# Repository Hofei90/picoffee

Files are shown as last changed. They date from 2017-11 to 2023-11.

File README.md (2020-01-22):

# picoffee
## Kurzbeschreibung
Die Software picoffee steuert die Freigabe für eine Kaffeemaschine bei Anmeldung eines Benutzers mittels 
RFID Chip und ausreichendem Guthaben.
Hardwareumsetzung kann natürlich unterschiedlich ausgeführt sein. In diesem Projekt ist es so realisiert, dass die 
Widerstände der Tastenplatine der Kaffeemaschine entlötet worden sind und diese über Relais zugeschaltet werden, 
gesteuert von picoffee.

## Software
### Benötigte Software
picoffee unterstützt Pythonversion >3.5.x

Benötigte Pythonmodule sind in der _requirements.txt_ gelistet.
 
### Installation
Paket unter gewünschten Verzeichnis abspeichern.

Zum Start von picoffee direkt die Datei _picoffee.py_ starten. Ein Autostart kann z.B mittels Systemd gelöst werden.
Beispiel siehe unter _picoffee.service_

## Komplette Projektvorstellung
Komplette Projektvorstellung unter: https://forum-raspberrypi.de/forum/thread/32856-kaffeemaschine-automatische-abrechnung/

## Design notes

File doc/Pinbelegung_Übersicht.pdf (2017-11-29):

Verwendung | Name | BCM | Pin Pin | BCM | Name | Verwendung
3,3V | 3,3V | - | 1 | 2 | - | 5V | 5V
LCD I²C | SDA | 2 | 3 | 4 | - | 5V | 5V
LCD I²C | SCL | 3 | 5 | 6 | - | GND | GND
| GPIO7 | 4 | 7 | 8 | 14 | TxD
GND | GND | - | 9 10 | 15 | RxD
GPIO0 | 17 | 11 12 | 18 | GPIO1
GPIO2 | 27 | 13 14 | - | GND | GND
GPIO3 | 22 | 15 16 | 23 | GPIO4
3,3V | 3,3V | - | 17 18 | 24 | GPIO5
RF522_MOSI | MOSI | 10 | 19 20 | - | GND | GND
RF522_MISO | MISO | 9 | 21 22 | 25 | GPIO6 | RF522_RST
RF522_SCK | SCLK | 11 | 23 24 | 8 | CE0 | RF522_SDA
GND | GND | - | 25 26 | 7 | CE1 | I_Mahlwerk
I²C | ID_SD | 0 | 27 28 | 12 | ID_SC | I²C
I_Wasser | GPIO21 | 5 | 29 30 | - | GND | GND
O_Freigabe | GPIO22 | 6 | 31 32 | 12 | GPIO26 | I_Taster_minus
O_RGB_R | GPIO23 | 13 | 33 34 | - | GND | GND
O_RGB_G | GPIO24 | 19 | 35 36 | 16 | GPIO27 | I_Taster_plus
O_RGB_B | GPIO25 | 26 | 37 38 | 20 | GPIO28 | I_TasterM
GND | GND | - | 39 40 | 21 | GPIO29 | I_TasterOk
Freie Pins | 9
Verwendete Pin | 31

Pinbelegung Kaffeekontrolle

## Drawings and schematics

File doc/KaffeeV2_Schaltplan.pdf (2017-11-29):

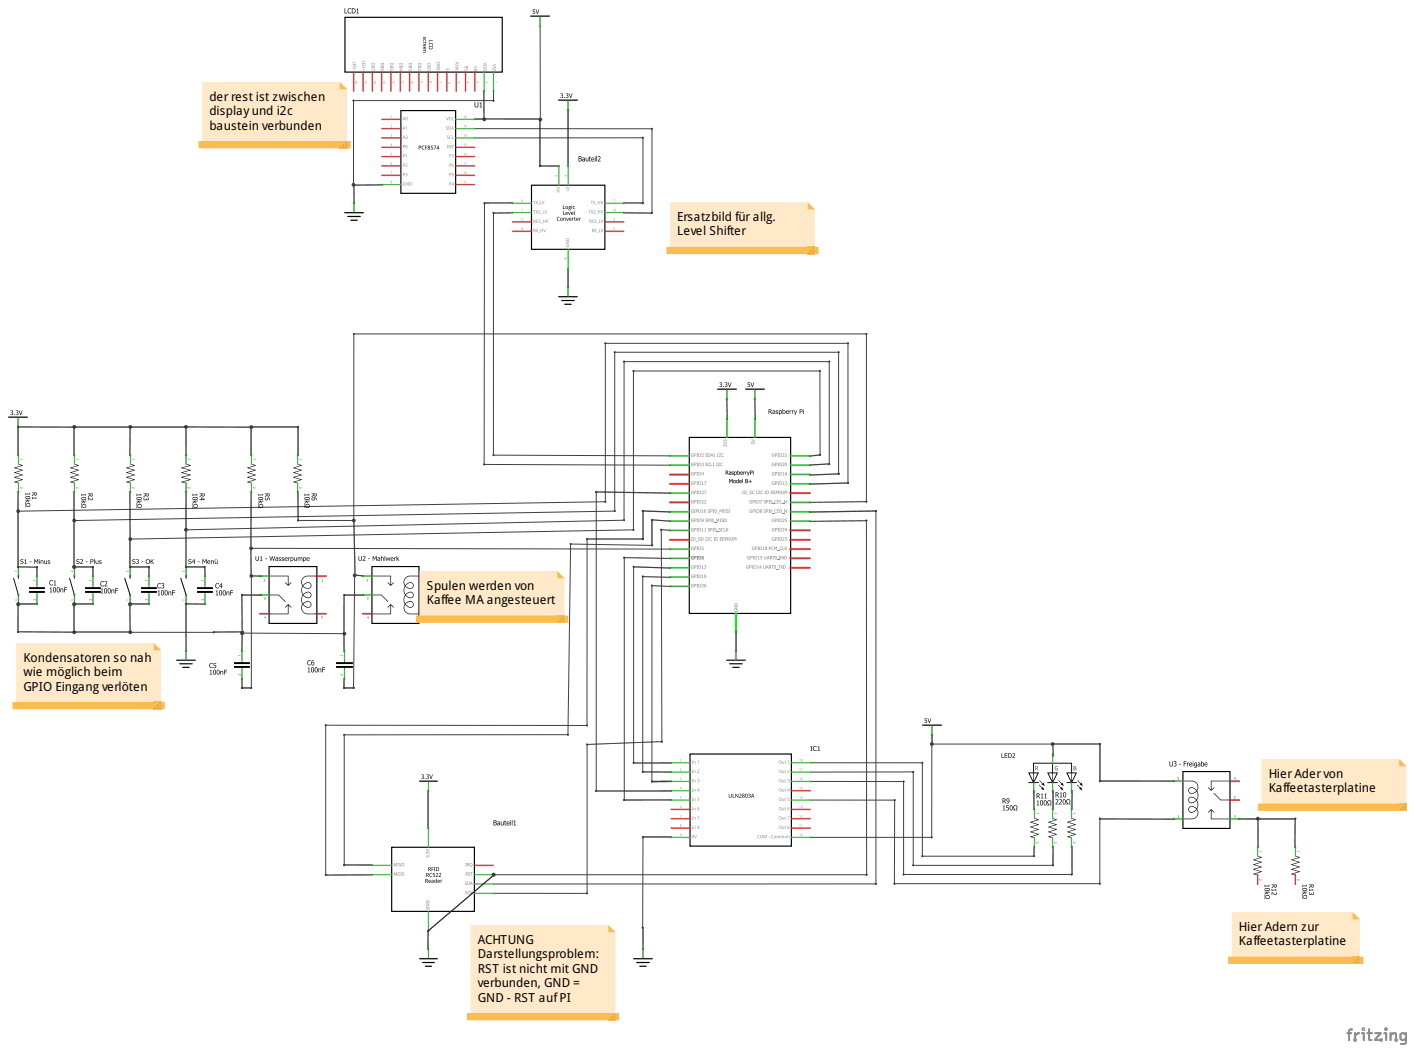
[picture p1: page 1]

derrest ist zwischen
display und i2c
baustein verbunden

Ersatzbild für allg.
Level Shifter

Spulen werden von
Kaffee MA angesteuert

Kondensatoren so nah
wie möglich beim
GPIO Eingang verlöten

Hier Ader von
Kaffeetasterplatine

Hier Adern zur

ACHTUNG
Darstellungsproblem:
RST ist nicht mit GND
verbunden, GND =
GND - RST auf PI

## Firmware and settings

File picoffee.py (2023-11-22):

#!/usr/bin/python3
# -*- coding: utf-8 -*-
# Script zur Kaffeekontrolle

import datetime
import random
import shlex
import signal
import subprocess
import time
from pathlib import Path
from sys import exit

import gpiozero
import toml
from RPLCD.i2c import CharLCD
from pirc522 import RFID

import Xtendgpiozero.buttonxtendgpiozero as xgpiozero
import db_coffee_model as db
import mail_bei_aufladung
import messagebox.anzeige as MessageboxAnzeige
import messagebox.messagebox as messagebox
import setup_logging
import sonderzeichen


SKRIPTPFAD = Path(__file__).parent
MAILCONFIG = toml.load(SKRIPTPFAD / "mailconfig.toml")["mail"]
LOGGER = setup_logging.create_logger("picoffee", 10, SKRIPTPFAD)

db.database.initialize(db.peewee.SqliteDatabase(SKRIPTPFAD / "db_coffee.db3", **{}))

# GPIO Buttons
TASTERMINUS = xgpiozero.Button(12, pull_up=None, active_state=False)
TASTERPLUS = xgpiozero.Button(16, pull_up=None, active_state=False)
TASTERMENUE = xgpiozero.Button(20, pull_up=None, active_state=False)
TASTEROK = xgpiozero.Button(21, pull_up=None, active_state=False)
MAHLWERK = xgpiozero.Button(14, pull_up=None, active_state=False)
WASSER = xgpiozero.Button(5, pull_up=None, active_state=False)

# GPIO Output
TASTEN_FREIGABE = gpiozero.DigitalOutputDevice(6, initial_value=False)
RGBLED = gpiozero.RGBLED(13, 26, 19, active_high=True, initial_value=(1, 0, 0))

PIN_RST = 25
PIN_CE = 0
PIN_IRQ = 24


class Display:
    def __init__(self):
        self.lcd = CharLCD(i2c_expander='PCF8574', address=0x27, port=1, cols=16, rows=2, dotsize=8, charmap='A02',
                           auto_linebreaks=True, backlight_enabled=True)
        self.displayinhalt = None
        self.displayhistory = []

    def display_schreiben(self, zeile1, zeile2=None):
        self.__set_displayinhalt(zeile1, zeile2)
        zeile1 = str(zeile1)
        self.lcd.clear()
        if zeile2 is None:
            self.lcd.write_string(zeile1)
        else:
            zeile2 = str(zeile2)
            if len(zeile1) > 16 or len(zeile2) > 16:
                self.lcd.write_string(zeile1)
                time.sleep(2)
                self.lcd.clear()
                self.lcd.write_string(zeile2)
                time.sleep(2)
            else:
                self.lcd.write_string(zeile1 + "\n\r" + zeile2)

    def __set_displayinhalt(self, zeile1, zeile2):
        self.__set_displayhistory()
        self.displayinhalt = [zeile1, zeile2]

    def __set_displayhistory(self):
        self.displayhistory.append(self.displayinhalt)
        if len(self.displayhistory) > 10:
            del self.displayhistory[0]


class Account:
    def __init__(self, display, chip, kaffeepreis, rdr):
        self.display = display
        self.rdr = rdr
        self.uid = chip.uid
        self.vorname = chip.benutzer.vorname
        self.nachname = chip.benutzer.nachname
        self.kontostand = chip.benutzer.konto
        self.kaffeelimit = chip.benutzer.kaffeelimit
        self.rechte = chip.benutzer.rechte
        self.benutzer = chip.benutzer  # Peewee Objekt Model
        self.konfig_neu_laden = False
        self.menue = None
        self.menueposition = None
        self.kaffeepreis = kaffeepreis
        self.kaffeebezugszeit = None  # Debugvariable
        self.letzte_aktivzeit = datetime.datetime.now()
        check_alle_taster()
        self.__create_menue()

    def __create_menue(self):
        self.menue = [["Aufladen", self.m_aufladen],
                      ["Reinigung", self.m_reinigung],
                      ["Statistik", self.m_statistik],
                      ["Auszahlen", self.m_auszahlen],
                      ["Letzter Kaffee", self.m_lastkaffee],
                      ["Manuell buchen", self.m_kaffee_manuell_buchen],
                      ["Kaffee Limit", self.m_kaffeelimit]]
        if self.rechte == 1:
            self.menue.append(["Benutzer erstellen", self.me_benutzer_erstellen])
            self.menue.append(["Registrieren", self.me_registrieren])
            self.menue.append(["Chip L\357schen", self.me_chip_loeschen])  # \357=ö
            self.menue.append(["Benutzer L\357schen", self.me_benutzer_loeschen])
            self.menue.append(["Preis anpassen", self.me_preis_anpassen])
            self.menue.append(["Kasse angleichen", self.me_kasse_korrigieren])
            self.menue.append(["Entkalken", self.me_entkalken])
            self.menue.append(["Herunterfahren", self.me_herunterfahren])

    def startseite_schreiben(self):
        kaffee_anzeige = self.get_kaffeelimit_zustand()
        self.display.display_schreiben("Konto:{:.2f}EUR".format(self.kontostand),
                                       "{}".format(kaffee_anzeige))

    def menue_enter(self):
        entferne_kaffeefreigabe()
        self.menueposition = 0
        self.display.display_schreiben(self.menue[self.menueposition][0])

    def menue_up(self):
        self.menueposition += 1
        if self.menueposition >= len(self.menue):
            self.menueposition = 0
        self.display.display_schreiben(self.menue[self.menueposition][0])

    def menue_down(self):
        self.menueposition -= 1
        if self.menueposition < 0:
            self.menueposition = len(self.menue) - 1
        self.display.display_schreiben(self.menue[self.menueposition][0])

    def m_aufladen(self):
        check_alle_taster()
        betrag = 5.0
        self.display.display_schreiben("Aufladebetrag:", "{:.2f}".format(betrag) + "EUR")
        while True:
            if TASTERPLUS.check_status():
                betrag = betrag + 5.0
                self.display.display_schreiben("Aufladebetrag:", "{:.2f}".format(betrag) + "EUR")
            if TASTERMINUS.check_status():
                betrag = betrag - 5.0
                if betrag < 5:
                    betrag = 5.0
                self.display.display_schreiben("Aufladebetrag:", "{:.2f}".format(betrag) + "EUR")
            if TASTEROK.check_status():
                self.display.display_schreiben("Bitte " + "{:.2f}".format(betrag) + "EUR", "einzahlen")
                while True:
                    if TASTERMENUE.check_status():
                        self.display.display_schreiben("Abgebrochen", "")
                        return
                    if TASTEROK.check_status():
                        self.kontostand += betrag
                        self.kontostand = round(self.kontostand, 2)
                        self.benutzer.konto = self.kontostand
                        self.benutzer.save()
                        db.Config.update(kasse=db.Config.kasse + betrag).execute()
                        versende_mail(self, betrag)
                        schreiben_in_buch(self.benutzer, betrag, "aufladen")

                        self.display.display_schreiben("Betrag", "aufgeladen")
                        return
            if TASTERMENUE.check_status():
                self.display.display_schreiben("Abgebrochen", "")
                return

    def m_reinigung(self):
        self.display.display_schreiben("Reinigung", "eintragen?")
        while True:
            if TASTEROK.check_status():
                schreiben_in_reinigung(self.benutzer, "reinigung")
                self.display.display_schreiben("Eingetragen!")
                time.sleep(2)
                return
            if TASTERMENUE.check_status():
                self.display.display_schreiben("Abgebrochen", "")
                time.sleep(2)
                return
            time.sleep(0.2)

    def m_statistik(self):
        check_alle_taster()
        self.display.display_schreiben("Jahr <+>", "Gesamt <->")
        while True:
            if TASTERPLUS.check_status():
                timestamp = timestamp_jahr_generieren()
                anzahl, summe = get_kaffee_bezuge(timestamp)
                summe = round(summe, 2)
                self.display.display_schreiben("{} Kaffee zu".format(anzahl),
                                               "{} EUR".format(summe))
                time.sleep(4)
                break

            if TASTERMINUS.check_status():
                anzahl, summe = get_kaffee_bezuge()
                summe = round(summe, 2)
                self.display.display_schreiben("{} Kaffee zu".format(anzahl),
                                               "{} EUR".format(summe))
                time.sleep(4)
                break

    def m_auszahlen(self):
        check_alle_taster()
        betrag = zahlen_einstellen(self.display)
        self.display.display_schreiben("{:.2f}EUR von".format(betrag), "Kasse entnehmen")
        while True:
            if TASTERMENUE.check_status():
                self.display.display_schreiben("Abgebrochen")
                time.sleep(2)
                return
            if TASTEROK.check_status():
                db.Config.update(kasse=db.Config.kasse - betrag).execute()
                kassenstand = db.Config.select(db.Config.kasse).scalar()
                schreiben_in_buch(self.benutzer, betrag, "auszahlen")
                self.display.display_schreiben("Abgebucht", "Kasse: {:.2f}EUR".format(kassenstand))
                time.sleep(2)
                return

    def m_lastkaffee(self):
        check_alle_taster()
        benutzer = get_letzten_kaffee_bezug()
        name = "{} {}".format(benutzer.vorname, benutzer.nachname)
        self.display.display_schreiben("Letzter Kaffee:", "{:.{widght}}".format(name, widght=16))
        time.sleep(2)

    def m_kaffee_manuell_buchen(self):
        self.display.display_schreiben("Kaffee manuell", "verbuchen?")
        while True:
            if TASTEROK.check_status():
                kaffee_verbuchen(self, {"kaffeepreis": self.kaffeepreis})
                return
            if TASTERMENUE.check_status():
                self.display.display_schreiben("Abgebrochen")
                time.sleep(2)
                return

    def m_kaffeelimit(self):
        check_alle_taster()
        self.display.display_schreiben("Limit setzen:", self.kaffeelimit)
        while True:
            if TASTERMENUE.check_status():
                self.display.display_schreiben("Abgebrochen")
                time.sleep(2)
                return
            if TASTEROK.check_status():
                self.benutzer.kaffeelimit = self.kaffeelimit
                self.benutzer.save()
                self.display.display_schreiben("Neues Limit:", self.kaffeelimit)
                time.sleep(2)
                break
            if TASTERPLUS.check_status():
                self.kaffeelimit += 1
                if self.kaffeelimit > 16:
                    self.kaffeelimit = 0
                self.display.display_schreiben("Limit setzen:", self.kaffeelimit)
            if TASTERMINUS.check_status():
                self.kaffeelimit -= 1
                if self.kaffeelimit < 0:
                    self.kaffeelimit = 16
                self.display.display_schreiben("Limit setzen:", self.kaffeelimit)
            time.sleep(0.1)
        return

    def me_benutzer_erstellen(self):
        check_alle_taster()
        self.display.display_schreiben("Vorname")
        self.display.lcd.cursor_mode = "blink"
        reg_name = [""] * 16
        select = 0
        cursor_position = 0
        self.display.lcd.cursor_pos = (1, cursor_position)

        unterfunktion = 0
        vorname = None

        while True:
            if TASTERMENUE.check_status():
                if unterfunktion == 0:
                    vorname = string_generieren(reg_name)
                    reg_name = [""] * 16
                    self.display.display_schreiben("Nachname", "")
                    cursor_position = 0
                    self.display.lcd.cursor_pos = (1, cursor_position)

                if unterfunktion == 1:
                    if vorname != "":
                        nachname = string_generieren(reg_name)
                        db.Benutzer.create(vorname=vorname, nachname=nachname,
                                           kaffeelimit=0, rechte=0, konto=0)
                        self.display.lcd.cursor_mode = "hide"
                        self.display.display_schreiben(vorname, nachname)
                        time.sleep(2)
                        self.display.display_schreiben("erfolgreich", "registriert")
                        break
                unterfunktion += 1

            if TASTEROK.check_status():
                if select == 0:
                    self.display.lcd.cursor_mode = "line"
                    select = 1
                elif select == 1:
                    self.display.lcd.cursor_mode = "blink"
                    select = 0

            if TASTERPLUS.check_status():
                if select == 0:
                    if cursor_position == 15:
                        cursor_position = 0
                        self.display.lcd.cursor_pos = (1, cursor_position)
                    else:
                        cursor_position = cursor_position + 1
                        self.display.lcd.cursor_pos = (1, cursor_position)
                if select == 1:
                    if reg_name[cursor_position] == "":
                        if cursor_position != 0:
                            reg_name[cursor_position] = "a"
                        else:
                            reg_name[cursor_position] = "A"
                    else:
                        ord_zeichen = ord(reg_name[cursor_position]) + 1
                        if ord_zeichen == 91:
                            ord_zeichen = 32
                        elif ord_zeichen == 33:
                            ord_zeichen = 97
                        elif ord_zeichen == 123:
                            ord_zeichen = 65
                        reg_name[cursor_position] = chr(ord_zeichen)
                    self.display.lcd.write_string(reg_name[cursor_position])
                    self.display.lcd.cursor_pos = (1, cursor_position)

            if TASTERMINUS.check_status():
                if select == 0:
                    if cursor_position == 0:
                        cursor_position = 15
                        self.display.lcd.cursor_pos = (1, cursor_position)
                    else:
                        cursor_position = cursor_position - 1
                        self.display.lcd.cursor_pos = (1, cursor_position)
                if select == 1:
                    if reg_name[cursor_position] == "":
                        if cursor_position != 0:
                            reg_name[cursor_position] = "z"
                        else:
                            reg_name[cursor_position] = "Z"
                    else:
                        ord_zeichen = ord(reg_name[cursor_position]) - 1
                        if ord_zeichen == 96:
                            ord_zeichen = 32
                        elif ord_zeichen == 31:
                            ord_zeichen = 90
                        elif ord_zeichen == 64:
                            ord_zeichen = 122
                        reg_name[cursor_position] = chr(ord_zeichen)
                    self.display.lcd.write_string(reg_name[cursor_position])
                    self.display.lcd.cursor_pos = (1, cursor_position)
            time.sleep(0.2)

    def me_registrieren(self):
        check_alle_taster()
        benutzer = benutzer_auswaehlen(self.display)
        if benutzer is None:
            return
        self.display.display_schreiben("Neuen Chip", "einlesen")
        nicht_abgebrochen = True
        while nicht_abgebrochen:
            if TASTERMENUE.check_status():
                self.display.display_schreiben("Abgebrochen")
                nicht_abgebrochen = False
            user = rfid_read(self.rdr)
            if user is not None:
                user_datensatz = user_check(user)
                if user_datensatz is None:
                    uid = user
                    db.Chip.create(uid=uid, benutzer=benutzer)
                    self.display.display_schreiben("Registrierung abgeschlossen")
                    break
                else:
                    self.display.display_schreiben("Chip schon", "registriert")
                    led_rot()
                    time.sleep(2)
                    self.display.display_schreiben("Neuen Chip", "einlesen")
                    led_blau()
            time.sleep(0.2)
        time.sleep(2)

    def me_chip_loeschen(self):
        check_alle_taster()
        self.display.display_schreiben("Chip", "entfernen")
        benutzer = benutzer_auswaehlen(self.display)
        if benutzer is not None:
            self.display.display_schreiben("Auswahl:", "Chip entfernen?")
            time.sleep(2)
            self.display.display_schreiben(benutzer.vorname, benutzer.nachname)
            while True:
                if TASTEROK.check_status():
                    db.Chip.delete().where(db.Chip.benutzer == benutzer).execute()
                    self.display.display_schreiben("Chip", "entfernt")
                    time.sleep(2)
                    return

                if TASTERMENUE.check_status():
                    self.display.display_schreiben("Abgebrochen")
                    time.sleep(2)
                    return

    def me_benutzer_loeschen(self):
        check_alle_taster()
        self.display.display_schreiben("Benutzer", "entfernen")
        time.sleep(2)
        self.display.display_schreiben("Auswahl treffen", "+-ok Taster")
        TASTEROK.wait_for_press()
        benutzer = benutzer_auswaehlen(self.display)
        if benutzer is None:
            return
        check_alle_taster()
        self.display.display_schreiben("AUSWAHL:")
        TASTEROK.wait_for_press()
        check_alle_taster()
        self.display.display_schreiben(benutzer.vorname, benutzer.nachname)
        TASTEROK.wait_for_press()
        check_alle_taster()
        self.display.display_schreiben("Restguthaben:", "{:.2f}EUR".format(benutzer.konto))
        TASTEROK.wait_for_press()
        check_alle_taster()
        self.display.display_schreiben("Betrag", "auszahlen")
        TASTEROK.wait_for_press()
        check_alle_taster()
        self.display.display_schreiben("Abbrechen mit", "Men\365taster")  # \365 = ü
        check_alle_taster()
        while True:
            if TASTERMENUE.check_status():
                self.display.display_schreiben("Abgebrochen", "")
                time.sleep(2)
                return
            if TASTEROK.check_status():
                unbekannter_user = get_or_create_unbekannter_user()
                db.Buch.update(benutzer=unbekannter_user).where(db.Buch.benutzer == benutzer).execute()
                db.Config.update(kasse=db.Config.kasse - benutzer.konto).execute()
                db.Reinigung.update(benutzer=unbekannter_user).where(db.Reinigung.benutzer == benutzer).execute()
                db.Chip.delete().where(db.Chip.benutzer == benutzer).execute()
                db.Benutzer.delete().where(db.Benutzer.id == benutzer.id).execute()
                self.display.display_schreiben("Benutzer", "gel\357scht")
                time.sleep(2)
                return
            time.sleep(0.2)

    def me_preis_anpassen(self):
        check_alle_taster()
        self.display.display_schreiben("Preis:", "{:.2f}".format(self.kaffeepreis) + "EUR")
        while True:
            if TASTERMINUS.check_status():
                if self.kaffeepreis <= 0.00:
                    pass
                else:
                    self.kaffeepreis -= 0.05
                    self.kaffeepreis = round(self.kaffeepreis, 2)
                    self.display.display_schreiben("Preis:", "{:.2f}".format(self.kaffeepreis) + "EUR")

            if TASTERPLUS.check_status():
                if self.kaffeepreis >= 1.00:
                    pass
                else:
                    self.kaffeepreis = self.kaffeepreis + 0.05
                    self.kaffeepreis = round(self.kaffeepreis, 2)
                    self.display.display_schreiben("Preis:", "{:.2f}".format(self.kaffeepreis) + "EUR")

            if TASTEROK.check_status():
                db.Config.update(kaffeepreis=self.kaffeepreis).execute()
                self.konfig_neu_laden = True
                return

            if TASTERMENUE.check_status():
                self.display.display_schreiben("Abgebrochen")
                return

    def me_kasse_korrigieren(self):
        """
        Differenzbetrag = Hardwarekasse - Softwarekasse
        Bsp: 15 - 14 = 1 (Differenzbetrag)
        Somit +1 EUR erforderlich damit Software mit Hardware Kasse übereinstimmt
        :return:
        """
        check_alle_taster()
        self.display.display_schreiben("Differenzbetrag", "eingeben")
        time.sleep(2)
        betrag = zahlen_einstellen(self.display)
        self.display.display_schreiben("S-K verringern -", "S-K erh\357hen +")
        while True:
            if TASTERMENUE.check_status():
                self.display.display_schreiben("Abgebrochen")
                time.sleep(2)
                return
            if TASTERPLUS.check_status():
                buch_typ = "korrektur_plus"
                break
            if TASTERMINUS.check_status():
                betrag *= -1
                buch_typ = "korrektur_minus"
                break
            time.sleep(0.1)
        db.Config.update(kasse=db.Config.kasse + betrag).execute()
        schreiben_in_buch(self.benutzer, abs(betrag), buch_typ)
        datensatz = konfiguration_laden()
        kasse = datensatz[1]
        self.display.display_schreiben("Verbucht", "Kasse: {:.2f}EUR".format(kasse))
        time.sleep(2)
        return
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

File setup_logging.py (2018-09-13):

#!/usr/bin/python3
"""
Beschreibung:
Hilfskript zum Erstellen einer logging Instanz in Abhängigkeit, ob das Skript manuell gestartet worden ist oder
ob das Skript per Service Unit gestartet wurde
Abhängig dessen wird entweder die Logging Instanz mit einem JournalHandler erstellt (Service Unit)
oder mit einem StreamHandler (manuell)

Author: Hofei
Datum: 03.08.2018
Version: 0.1
"""
import logging
import os
import shlex
import subprocess

from systemd import journal


def __setup_logging(loglevel, frm, startmethode, unitname, pfad):
    """
    Erstellt die Logger Instanz für das Skript
    """
    logger = logging.getLogger()
    logger.setLevel(loglevel)
    logger.handlers = []
    if startmethode == "auto":
        log_handler = journal.JournalHandler(SYSLOG_IDENTIFIER=unitname)

    else:
        fehlerlog = os.path.join(pfad, "{}.log".format(unitname))
        log_handler = logging.FileHandler(fehlerlog)
    log_handler.setLevel(loglevel)
    log_handler.setFormatter(frm)
    logger.addHandler(log_handler)
    return logger


def __get_service_unit_pid(unitname):
    """Ermittelt ob  das ausführende Skript mit einer Service Unit gestartet worden ist, wenn ja so ist das
    Ergebnis (pid_service_unit) != 0"""
    cmd = "systemctl show -p MainPID {}".format(unitname)
    cmd = shlex.split(cmd)
    antwort = subprocess.run(cmd, stdout=subprocess.PIPE)
    ausgabe = antwort.stdout
    # strip entfernt \n, split teilt am = in eine Liste und [1] weißt die Zahl in die Variable zu
    pid_service_unit = int(ausgabe.decode().strip().split("=")[1])
    return pid_service_unit


def __get_startmethode(unitname):
    """Verglicht die PID vom skript mit der pid Service Unit Prüfung
    wenn die Nummern gleich sind wird auf auto gestellt, wenn nicht auf manuell"""
    pid_service_unit = __get_service_unit_pid(unitname)
    pid_skript = os.getpid()
    if pid_service_unit == pid_skript:
        startmethode = "auto"
    else:
        startmethode = "manuell"
    return startmethode


def __set_loggerformat(startmethode):
    """Stellt die passende Formattierung ein"""
    if startmethode == "auto":
        frm = logging.Formatter("%(levelname)s: %(message)s", "%d.%m.%Y %H:%M:%S")
    else:
        frm = logging.Formatter("%(asctime)s %(levelname)s: %(message)s", "%d.%m.%Y %H:%M:%S")
    return frm


def create_logger(unitname, loglevel, pfad):
    """Dies ist die aufzurufende Funktion bei der Verwendung des Moduls von außen
    Liefert die fertige Logging Instanz zurück"""
    startmethode = __get_startmethode(unitname)
    frm = __set_loggerformat(startmethode)
    return __setup_logging(loglevel, frm, startmethode, unitname, pfad)


if __name__ == "__main__":
    logger = create_logger("testunit", 10, "")
    logger.debug("Testnachricht")

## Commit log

2017-06-05 Gitlab INIT
    [Kaffee.fzz, Log_Matrix.xlsx, Pinbelegung_Übersicht.xlsx]
2017-06-08 Pinbelegung_Übersicht.pdf : Komprimierte Ansicht
    KaffeeV2.fzz: Neuen Schaltplan erstellt
    KaffeeV2_Schaltplan.pdf: Export Ausgabe in PDF
    [KaffeeV2.fzz]
2017-06-13 Schaltplan neu erstellt
    [KaffeeV2.fzz]
2017-06-28 doc erstellt
    [Kaffee.fzz, KaffeeV2.fzz, Log_Matrix.xlsx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]
2017-08-19 Anmeldezeit verändert, Tastenfreigabe wird noch während der Anmeldung entfernt. Logout per OK Taster integriert
2017-11-29 Beginn V2
    [KaffeeV2.fzz]
2018-09-13 xtend modul while entfernt - alternative geschrieben und getestet
2018-12-12 start der Messagebox
2018-12-13 wiederholte Anzeige der Nachrichten
2019-03-15 Fehler behoben: nach Entkalken wird angezeigt Mahlwerk aktiv und oder Heißwasser läuft.
    [picoffee.py]
2023-11-21 change Pin 7 to 14
